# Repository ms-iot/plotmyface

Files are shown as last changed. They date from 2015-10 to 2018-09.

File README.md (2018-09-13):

# Plot My Face using Travelling Salesperson Art
This project demonstrates Direct Memory Mapping and Hybrid applications which leverage Arduino libraries on Windows 10 IoT Core for Raspberry Pi. 

The key elements of this project are:

* Using camera to capture an image, with a live preview
* Using Xaml UI to display intermediate stages of the plot
* Dither the input image to generate a series of dots
* Use a travelling salesperson algorithm to connect the dots using line segments
* Use the line segements to drive an H-Bot style carteisian plotter
* Drive steppers using the Arduino library [AccelStepper](http://www.airspayce.com/mikem/arduino/AccelStepper/) written by Mike McCauley.

# Bill of Materials
* Raspberry Pi 2
* [MakeBlock Lab Kit](http://www.makeblock.cc/lab-robot-kit-blue-no-electronics/) (or equivelent parts)
* [MakeBlock Long Rails](http://www.makeblock.cc/beam0824-496-blue-6-pack/)
* 2x [SparkFun Big Easy Driver](https://www.sparkfun.com/products/12859)
* (optional) [Adafruit permaproto HAT for Raspberry Pi 2](http://www.adafruit.com/products/2310)
* Video Camera which supports USB Video Class driver.
* 3d Printed Idle Wheel

# Software Components
* Windows 10 IoT Core, build 10556 or later
* [Win2D for Windows 10](https://github.com/Microsoft/win2d)
* [AccelStepper](http://www.airspayce.com/mikem/arduino/AccelStepper/)
* [Travelling Salesman Algorithm](http://www.codeproject.com/Articles/792887/Travelling-Salesman-Genetic-Algorithm)

# Explaination of the hardware build
The hardware for this plotter is configured as an H-Bot cartesian frame. An HBot uses a single long toothed belt and two stepper motors to drive the X and Y axes. The configuration has the benefit that both of the stepper motors are mounted to the frame, which means the central carriage is very light and can move exceptionally fast. The downside of the HBot it is not balanced - if the Y axis is not extremely rigid, there can be racking. The simplicity of this design makes it a quick and easy build.

## Steppers
The two steppers work together to drive the X and Y axes, instead of each motor controlling a single axis. The formula for converting from axis steps to multi-motor steps are:

```aStepper = xStep + yStep```
```bStepper = xStep - yStep```

# Software
The application that drives this project is a hybrid application - it uses a C# and Xaml host, with a C++/CX Windows component which hosts the Arduino wiring code.

## Capture
The Capture pipeline uses MediaCapture in the Windows.Media.Capture namespace. This component is associated with a live preview window in xaml. When the user selects capture, a picture is saved to storage then processing begins.

## Dither
The image is then processed using a Floyd-Steinberg Two-dimensional error diffusion dithering algorithm. It is currently configured to reduce the number of points for speed purposes. This can be controled by adjusting ```kBWThreshold``` in ```Dithering.cs```

## Travelling Salesperson
The points in the dither are connected using a Travelling Salesperson Algorithm - generating [TSP Art](http://wiki.evilmadscientist.com/TSP_art). The agorithm is currently configured for expedient rendering, not an optimal solution. If you want to reconfigure this, instructs are available in ```TravellingSalesmanAlgorithm.cs```

## Drawing
Once the TSP is generated, the [Win2D](https://github.com/Microsoft/win2d) canvas draws the TSP, with progress. The datastructure backing the rendering is used to generate the toolpath - and ultimately the stepper profiles using [AccelStepper](http://www.airspayce.com/mikem/arduino/AccelStepper/).

# left as an exercise to the reader
There are many things that can be done with this project:
* Convert the H-Bot to [CoreXY](http://corexy.com/) which balances the load better
* Use a [rigid plotter frame](http://www.makeblock.cc/xy-plotter-robot-kit/)
* [Laser Engraving](http://www.makeblock.cc/laser-engraver-upgrade-pack-500mw-for-xy-plotter-robot-kit-v2-0/)
* Parallelize dithering and TSP generation

===

This project has adopted the [Microsoft Open Source Code of Conduct](http://microsoft.github.io/codeofconduct). For more information see the [Code of Conduct FAQ](http://microsoft.github.io/codeofconduct/faq.md) or contact [opencode@microsoft.com](mailto:opencode@microsoft.com) with any additional questions or comments.

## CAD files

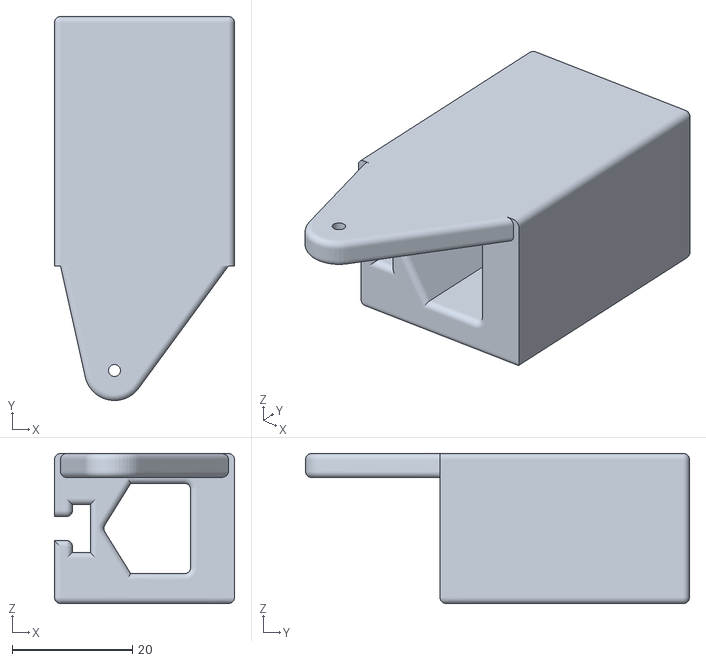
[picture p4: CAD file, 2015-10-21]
Hardware/PenHolder.stl
30.0 x 64.0 x 25.0

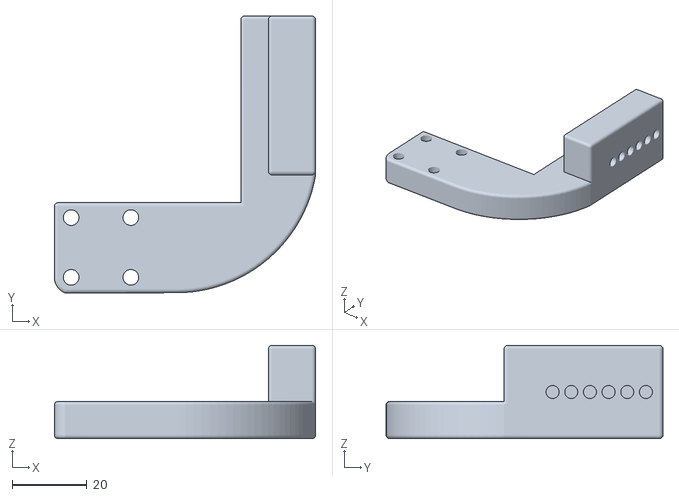
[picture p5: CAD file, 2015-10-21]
Hardware/Rigid Arm.stl
70.0 x 74.2 x 25.0

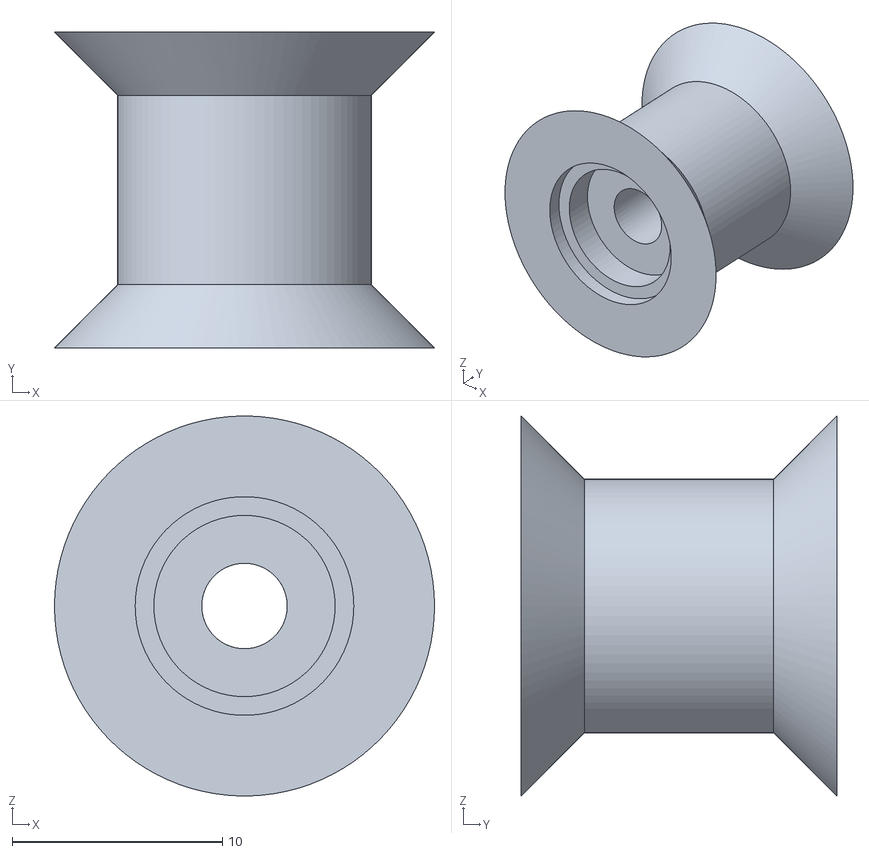
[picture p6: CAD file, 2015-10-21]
Hardware/Idler.stl
18.1 x 15.0 x 18.1

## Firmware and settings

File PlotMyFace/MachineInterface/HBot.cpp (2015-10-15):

#include "HBot.h"

namespace MachineInterface
{

	const int kHomeBackoff = 5;

	HBot::HBot(
		int aStepPin, int aDirPin, int aEnPin,
		int bStepPin, int bDirPin, int bEnPin,
		int xHome, int yHome)
		: _aStepper(1, aStepPin, aDirPin)
		, _bStepper(1, bStepPin, bDirPin)
		, _state(BotState_Idle)
	{
		_aStepPin = aStepPin;
		_aDirPin = aDirPin;
		_aEnPin = aEnPin;
		_bStepPin = bStepPin;
		_bDirPin = bDirPin;
		_bEnPin = bEnPin;
		_xHome = xHome;
		_yHome = yHome;

		pinMode(_aStepPin, OUTPUT);
		pinMode(_aDirPin, OUTPUT);
		pinMode(_aEnPin, OUTPUT);
		pinMode(_bDirPin, OUTPUT);
		pinMode(_aStepPin, OUTPUT);
		pinMode(_bEnPin, OUTPUT);
		pinMode(_xHome, INPUT_PULLUP);
		pinMode(_yHome, INPUT_PULLUP);

		disable();

		setMaxValues();
	}

	void HBot::setInfo(
		int widthMM, int heightMM,
		int stepsPerMM)
	{
		_widthMM = widthMM;
		_heightMM = heightMM;
		_stepsPerMM = stepsPerMM;
	}

	void HBot::enable()
	{
		digitalWrite(_aEnPin, 0);
		digitalWrite(_bEnPin, 0);
	}

	void HBot::disable()
	{
		digitalWrite(_aEnPin, 1);
		digitalWrite(_bEnPin, 1);
	}


	void HBot::setMaxValues()
	{
		_aStepper.setAcceleration(70000);
		_bStepper.setAcceleration(70000);
		_aStepper.setMaxSpeed(80000);
		_bStepper.setMaxSpeed(80000);
	}

	void HBot::home()
	{
		if (atXStop() &&
			atYStop())
		{
			// At Physical stops, so backoff.
			setMaxValues();
			move(kHomeBackoff, kHomeBackoff);
		}
		else
		{

			_aStepper.setAcceleration(800);
			_bStepper.setAcceleration(800);
			_aStepper.setMaxSpeed(800);
			_bStepper.setMaxSpeed(800);
			if (!atXStop())
			{
				moveRelative(-_widthMM, 0);
				_state = BotState_HomingX;
			}
			else
			{
				moveRelative(0, -_heightMM);
				_state = BotState_HomingY;
			}
		}
	}

	void HBot::step(int64 stepA, int64 stepB)
	{
		_aStepper.moveTo((long)stepA);
		_bStepper.moveTo((long)stepB);

		_state = BotState_Moving;
	}


	void HBot::move(int xMM, int yMM)
	{
		long aSteps = (yMM + xMM) * _stepsPerMM;
		long bSteps = (yMM - xMM) * _stepsPerMM;
		_aStepper.moveTo(aSteps);
		_bStepper.moveTo(bSteps);

		_state = BotState_Moving;
	}

	void HBot::moveRelative(int xMM, int yMM)
	{
		long aSteps = (yMM + xMM) * _stepsPerMM;
		long bSteps = (yMM - xMM) * _stepsPerMM;
		_aStepper.move(aSteps);
		_bStepper.move(bSteps);

		_state = BotState_Moving;
	}

	bool HBot::run()
	{
		bool running = false;
		int64 xPos = currentXPosMM();
		int64 yPos = currentYPosMM();

		if (_state != BotState_Idle)
		{
			if (_state == BotState_HomingX)
			{
				if (atXStop())
				{
					_aStepper.setCurrentPosition(0);
					_bStepper.setCurrentPosition(0);
					move(kHomeBackoff, 0);
					_state = BotState_HomingXBackoff;
				}
			}
			else if (_state == BotState_HomingXBackoff)
			{
				if (xPos >= kHomeBackoff)
				{
					_aStepper.setCurrentPosition(0);
					_bStepper.setCurrentPosition(0);
					move(0, -_heightMM);
					_state = BotState_HomingY;
				}
			}
			else if (_state == BotState_HomingY)
			{
				if (atYStop())
				{
					_aStepper.setCurrentPosition(0);
					_bStepper.setCurrentPosition(0);
					move(kHomeBackoff, kHomeBackoff);
					_state = BotState_HomingYBackoff;
				}
			}
			else if (_state == BotState_HomingYBackoff)
			{
				if (yPos >= kHomeBackoff)
				{
					setMaxValues();
				}
			}

			bool aFinished = _aStepper.run() == false;
			bool bFinished = _bStepper.run() == false;

			if (aFinished && bFinished)
			{
				_state = BotState_Idle;
				running = false;
			}
			else
			{
				running = true;
			}
		}

		return running;
	}

};

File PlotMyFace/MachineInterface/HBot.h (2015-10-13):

#pragma once
#include "AccelStepper.h"

namespace MachineInterface
{
	public ref class HBot sealed
	{
		typedef enum
		{
			BotState_Idle = 0,
			BotState_HomingX,
			BotState_HomingXBackoff,
			BotState_HomingY,
			BotState_HomingYBackoff,
			BotState_Moving
		} BotState;
		int _aStepPin;
		int _aDirPin;
		int _aEnPin;
		int _bStepPin;
		int _bDirPin;
		int _bEnPin;
		int _xHome;
		int _yHome;

		int _widthMM;
		int _heightMM;
		int _stepsPerMM;

		BotState _state;

		AccelStepper _aStepper;
		AccelStepper _bStepper;
		void setMaxValues();
	public:
		HBot(int aStepPin, int aDirPin, int aEnPin,
			int bStepPin, int bDirPin, int bEnPin,
			int xHome, int yHome);
		void home();
		void step(int64 stepA, int64 stepB);
		void move(int xMM, int yMM);
		void moveRelative(int xMM, int yMM);
		void setInfo(
			int widthMM, int heightMM,
			int stepsPerMM);
		bool run();

		void enable();
		void disable();

		int64 currentXPosMM()	// in mm
		{
			long aSteps = _aStepper.currentPosition();
			long bSteps = _bStepper.currentPosition();

			return (aSteps - bSteps) / 2 / _stepsPerMM;
		}

		int64 currentYPosMM()
		{
			long aSteps = _aStepper.currentPosition();
			long bSteps = _bStepper.currentPosition();

			return (aSteps + bSteps) / 2 / _stepsPerMM;
		}

		bool atXStop()
		{
			return digitalRead(_xHome) == 0;
		}

		bool atYStop()
		{
			return digitalRead(_yHome) == 0;
		}

		bool isRunning()
		{
			return _state != BotState_Idle;
		}
	};


};

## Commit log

2015-10-13 Adding Machine interface & wiring code
2015-10-13 No longer using CaptureUI
    [HBot.cpp, HBot.h]
2015-10-13 Improve homing
2015-10-14 Switch to Win2D for canvas, implement play by play
2015-10-15 Include AccelStepper correctly
    [project.cfg]
2015-10-15 Update Readme, upload idle wheel
    [Idler.stl]
2015-10-21 Add Pen holder hardware
    [PenHolder.stl, Rigid Arm.stl]
